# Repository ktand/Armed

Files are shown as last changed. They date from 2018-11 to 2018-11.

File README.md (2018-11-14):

# Armed 3D Printer Controller

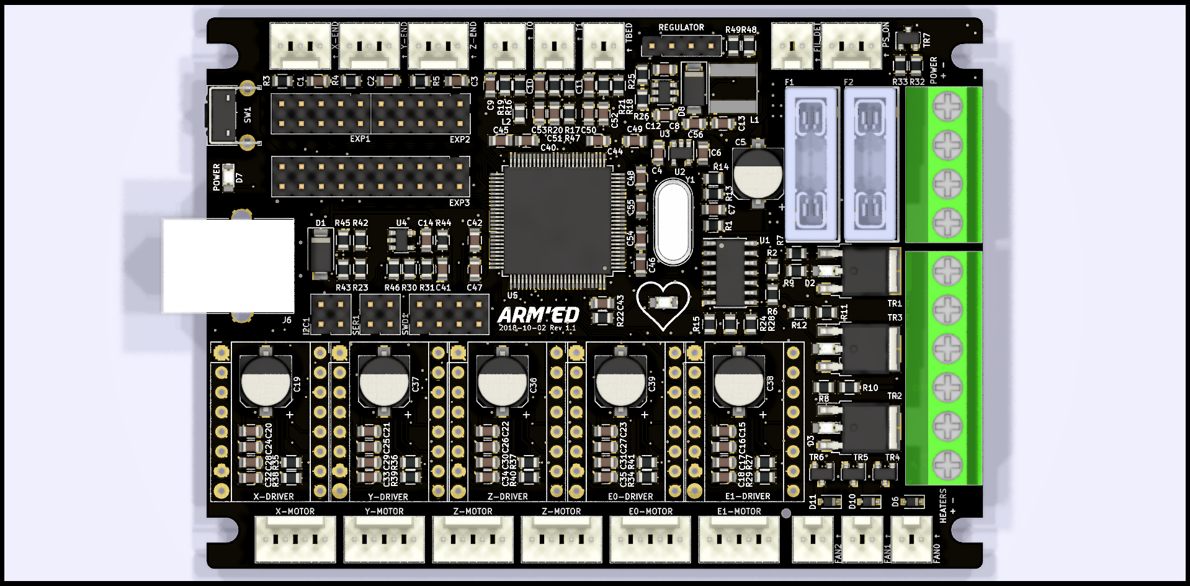
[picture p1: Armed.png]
Armed 1.1


## Features

* 32bit STM32F407VET6 
  * 168MHz 
  * 512kB Flash 
  * 192kB RAM 
* Power supply from 12-24V 
* Dual power inputs with separate fuses 
  * One for one of the high current outputs and the other one for the rest 
* Up to 5 steppers 
  * Dual outputs for one stepper for use with dual stepper Z-axis 
* 3 high current outputs 
* 3 fan outputs 
* 3 temperature sensors inputs 
* 3 endstops inputs 
* Filament runout detection 
* LCD display header 
* USB support 
* 10 extension pins 
* Support for TMC2130 SPI 
* 12-24V supply 
* I2C, SPI and UART extension ports 
* SWD header 
* Stepper configuration using solder jumpers 
* Einsy Rambo Form Factor (100x71mm) 

## Schematic and PCB Design

Designed using [Kicad 5.0](http://kicad-pcb.org/).

## Compatibilty

Arduino compatbile using the [Arduino Core STM32](https://github.com/stm32duino/Arduino_Core_STM32) and working with the [Marlin 2.0 3D printer firmware](https://github.com/MarlinFirmware/Marlin/tree/bugfix-2.0.x).

## Board configuration and pinout

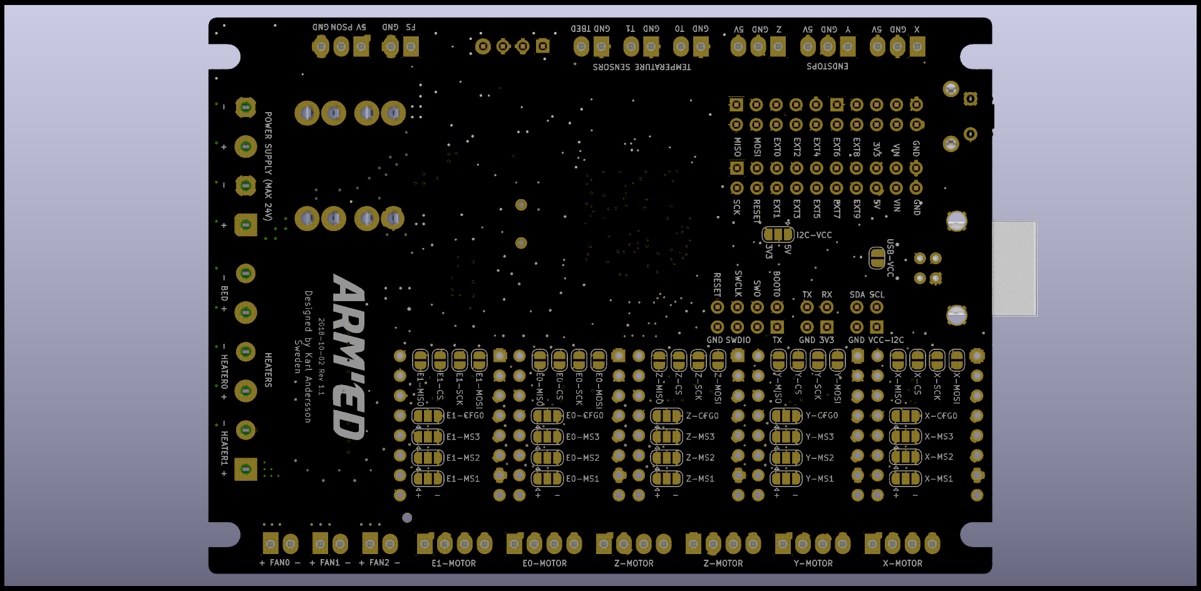
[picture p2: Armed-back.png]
Armed 1.1


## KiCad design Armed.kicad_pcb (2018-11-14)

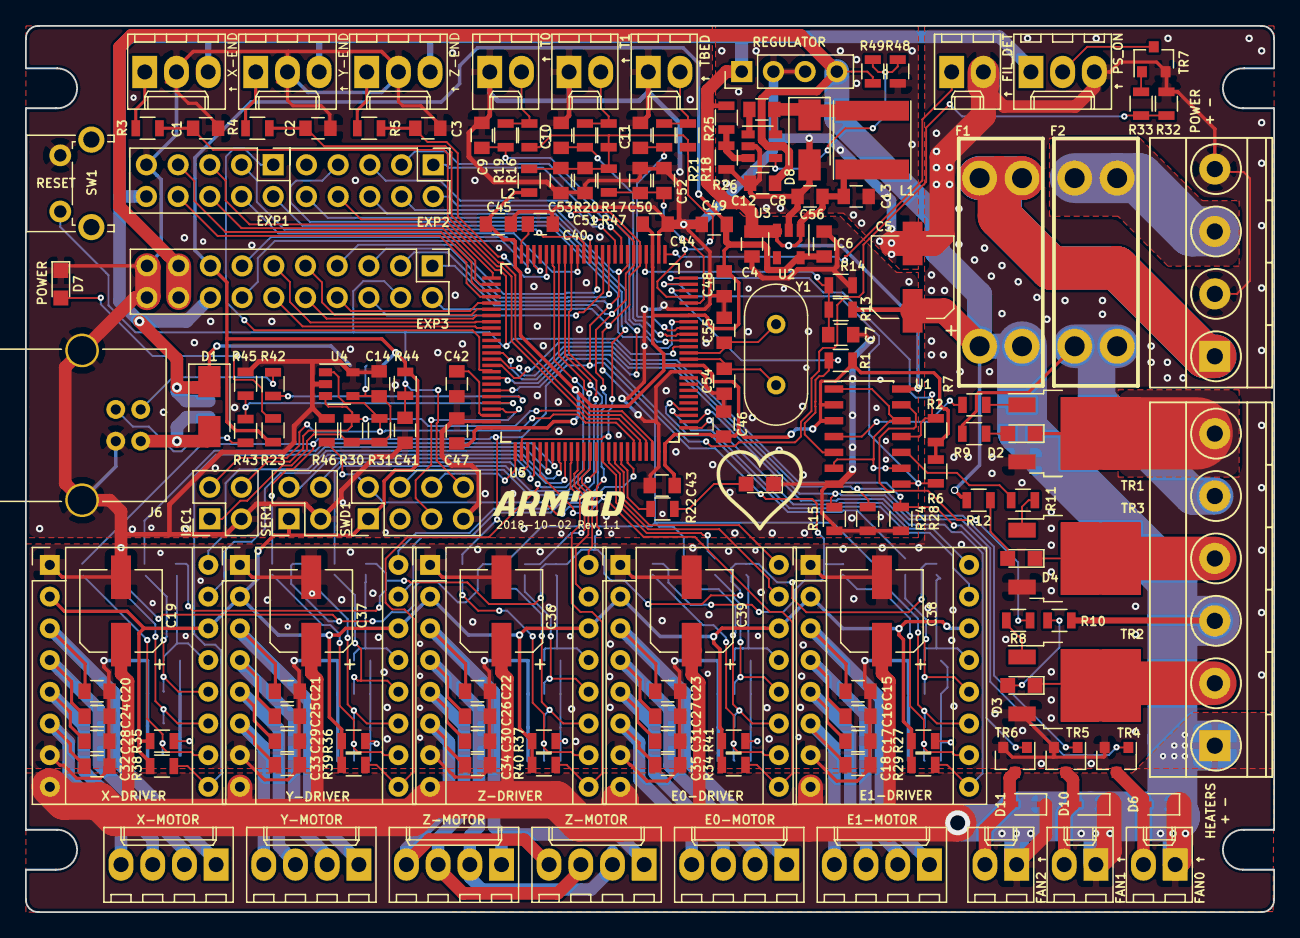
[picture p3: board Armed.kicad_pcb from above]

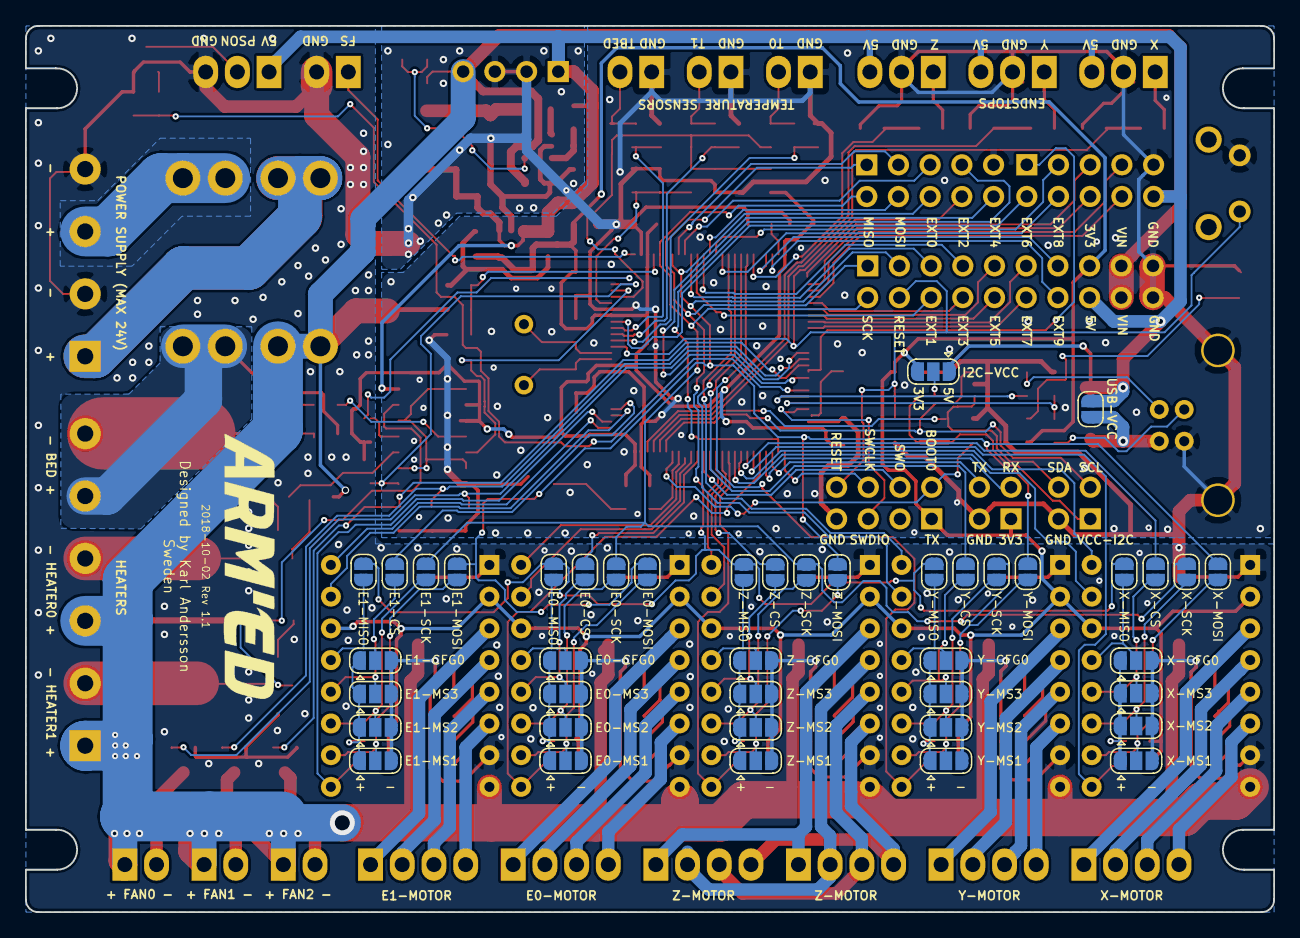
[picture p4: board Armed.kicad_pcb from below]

Board: 2 copper layers, 100.0 x 71.0 mm, 207 parts (42 on the bottom side), 165 nets.

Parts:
A1, A2, A3, A4, A5: Pololu_Breakout_A4988; Pololu_Breakout-16_15.2x20.3mm
C1, C2, C3: 10nF; C_0805
C4, C6: 1uF 16V X7R/X5R; C_0805
C5, C19, C36, C37, C38, C39: 100uF 35V; CP_Elec_6.3x5.8
C7, C12, C14, C41, C43, C44, C45, C46, C47, C48, C52, C53, C56: 100nF; C_0805
C8: 10uF 35V (X5R/X7R); C_0805
C9, C10, C11, C40, C42: 2.2uF; C_0805
C13: 10uF 16V (X5R/X7R); C_0805
C15, C16, C17, C18, C20, C21, C22, C23, C24, C25, C26, C27, C28, C29, C30, C31, C32, C33, C34, C35: 1nF; C_0805
C49: 10uF; C_0805
C50, C51: 1uF; C_0805
C54, C55: 20pF; C_0805
D1: BAT60J; D_SMA
D2, D3, D4, D5, D7: LED; LED_0805
D6, D10, D11: 1N4148WS; D_SOD-323
D8: B140-13-F; D_SMA
E0-MOT1, E1-MOT1: Conn_01x04_Male; Molex_KK-6410-04_04x2.54mm_Straight
EXP1, EXP2: Conn_02x05_Odd_Even; Pin_Header_Straight_2x05_Pitch2.54mm
EXP3: Conn_02x10_Odd_Even; Pin_Header_Straight_2x10_Pitch2.54mm
F1, F2: 3557-2; KEYSTONE-FUSE-3557-2
FAN1, FAN2, FAN3: Conn_01x02; Molex_KK-6410-02_02x2.54mm_Straight
FIL_DET1: Conn_01x02; Molex_KK-6410-02_02x2.54mm_Straight
I2C1: Conn_01x04; Pin_Header_Straight_2x02_Pitch2.54mm
J1: Conn_01x06; TerminalBlock_Phoenix_MKDS1.5-6pol
J2: Conn_01x04; TerminalBlock_Phoenix_MKDS1.5-4pol
J3, J4, J5: Conn_01x03; Molex_KK-6410-03_03x2.54mm_Straight
J6: USB_B
J7: Conn_01x04; Pin_Header_Straight_1x04_Pitch2.54mm
JP1: USB-VCC; SolderJumper-2_P1.3mm_Open_RoundedPad1.0x1.5mm
JP2: E1-MISO; SolderJumper-2_P1.3mm_Open_RoundedPad1.0x1.5mm
JP3: E1-MOSI; SolderJumper-2_P1.3mm_Open_RoundedPad1.0x1.5mm
JP4: E1-SCK; SolderJumper-2_P1.3mm_Open_RoundedPad1.0x1.5mm
JP5: E1-CS; SolderJumper-2_P1.3mm_Open_RoundedPad1.0x1.5mm
JP6: E1-CFG0; SolderJumper-3_P1.3mm_Open_RoundedPad1.0x1.5mm
JP7: E1-MS1; SolderJumper-3_P1.3mm_Open_RoundedPad1.0x1.5mm
JP8: E1-MS2; SolderJumper-3_P1.3mm_Open_RoundedPad1.0x1.5mm
JP9: E1-MS3; SolderJumper-3_P1.3mm_Open_RoundedPad1.0x1.5mm
JP10: E0-MISO; SolderJumper-2_P1.3mm_Open_RoundedPad1.0x1.5mm
JP11: E0-MOSI; SolderJumper-2_P1.3mm_Open_RoundedPad1.0x1.5mm
JP12: E0-SCK; SolderJumper-2_P1.3mm_Open_RoundedPad1.0x1.5mm
JP13: E0-CS; SolderJumper-2_P1.3mm_Open_RoundedPad1.0x1.5mm
JP14: X-MISO; SolderJumper-2_P1.3mm_Open_RoundedPad1.0x1.5mm
JP15: X-MOSI; SolderJumper-2_P1.3mm_Open_RoundedPad1.0x1.5mm
JP16: X-SCK; SolderJumper-2_P1.3mm_Open_RoundedPad1.0x1.5mm
JP17: X-CS; SolderJumper-2_P1.3mm_Open_RoundedPad1.0x1.5mm
JP18: Y-MISO; SolderJumper-2_P1.3mm_Open_RoundedPad1.0x1.5mm
JP19: Y-MOSI; SolderJumper-2_P1.3mm_Open_RoundedPad1.0x1.5mm
JP20: Y-SCK; SolderJumper-2_P1.3mm_Open_RoundedPad1.0x1.5mm
JP21: Y-CS; SolderJumper-2_P1.3mm_Open_RoundedPad1.0x1.5mm
JP22: Z-MISO; SolderJumper-2_P1.3mm_Open_RoundedPad1.0x1.5mm
JP23: Z-MOSI; SolderJumper-2_P1.3mm_Open_RoundedPad1.0x1.5mm
JP24: Z-SCK; SolderJumper-2_P1.3mm_Open_RoundedPad1.0x1.5mm
JP25: Z-CS; SolderJumper-2_P1.3mm_Open_RoundedPad1.0x1.5mm
JP26: E0-CFG0; SolderJumper-3_P1.3mm_Open_RoundedPad1.0x1.5mm
JP27: X-CFG0; SolderJumper-3_P1.3mm_Open_RoundedPad1.0x1.5mm
JP28: Y-CFG0; SolderJumper-3_P1.3mm_Open_RoundedPad1.0x1.5mm
JP29: Z-CFG0; SolderJumper-3_P1.3mm_Open_RoundedPad1.0x1.5mm
JP30: E0-MS1; SolderJumper-3_P1.3mm_Open_RoundedPad1.0x1.5mm
JP31: X-MS1; SolderJumper-3_P1.3mm_Open_RoundedPad1.0x1.5mm
JP32: Y-MS1; SolderJumper-3_P1.3mm_Open_RoundedPad1.0x1.5mm
JP33: Z-MS1; SolderJumper-3_P1.3mm_Open_RoundedPad1.0x1.5mm
JP34: X-MS2; SolderJumper-3_P1.3mm_Open_RoundedPad1.0x1.5mm
JP35: Y-MS2; SolderJumper-3_P1.3mm_Open_RoundedPad1.0x1.5mm
JP36: Z-MS2; SolderJumper-3_P1.3mm_Open_RoundedPad1.0x1.5mm
JP37: E0-MS2; SolderJumper-3_P1.3mm_Open_RoundedPad1.0x1.5mm
JP38: X-MS3; SolderJumper-3_P1.3mm_Open_RoundedPad1.0x1.5mm
JP39: Y-MS3; SolderJumper-3_P1.3mm_Open_RoundedPad1.0x1.5mm
JP40: Z-MS3; SolderJumper-3_P1.3mm_Open_RoundedPad1.0x1.5mm
JP41: E0-MS3; SolderJumper-3_P1.3mm_Open_RoundedPad1.0x1.5mm
JP42: I2C-VCC; SolderJumper-3_P1.3mm_Open_RoundedPad1.0x1.5mm
L1: 22uH NR6028T220M; L_Taiyo-Yuden_NR-60xx
L2: 7427920415; L_0805
PS_ON1: Conn_01x03; Molex_KK-6410-03_03x2.54mm_Straight
R1, R2, R6: 33k; R_0805
R3, R4, R5, R19, R20, R21, R29, R38, R39, R40, R41: 10k; R_0805
R7, R8, R11: 180; R_0805
R9, R10, R12, R14, R16, R17, R18, R27, R30, R31, R34, R35, R36, R37, R45: 4k7; R_0805
R13, R32, R48, R49: 47k; R_0805
R15, R22, R23, R24, R28, R33: 1k; R_0805
R25: 49.9k; R_0805
R26: 9.53k; R_0805
R42, R43: 20; R_0805
R44, R46: 100k; R_0805
R47: 47; R_0805
SER1: Conn_02x02; Pin_Header_Straight_2x02_Pitch2.54mm
SW1: SW_SPST; SW_Tactile_SPST_Angled_PTS645Vx31-2LFS
SWD1: Conn_02X04; Pin_Header_Straight_2x04_Pitch2.54mm
TEMP1, TEMP2, TEMP3: Conn_01x02; Molex_KK-6410-02_02x2.54mm_Straight
TR1, TR2, TR3: IPD036N04L; TO-252-2
TR4, TR5, TR6, TR7: PMV40UN2; SOT-23
U1: 74HCT02; SOIC-14_3.9x8.7mm_Pitch1.27mm
U2: AP2112K-3.3TRG1; SOT-23-5
U3: AOZ1282CI/AP3012; SOT-23-6
U4: 24LC32AT-I/OT; SOT-23-5
U5: STM32F407V(E-G)Tx; LQFP-100_14x14mm_Pitch0.5mm
X-MOT1: Conn_01x04_Male; Molex_KK-6410-04_04x2.54mm_Straight
Y1: 8MHz; Crystal_HC49-U_Vertical
Y-MOT1: Conn_01x04_Male; Molex_KK-6410-04_04x2.54mm_Straight
Z-MOT1, Z-MOT2: Conn_01x04_Male; Molex_KK-6410-04_04x2.54mm_Straight

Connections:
3V3_FAILURE: U1.1, U1.6, U1.9, U1.12
12V1: A1.8, A2.8, A3.8, A4.8, A5.8, C5.1, C8.1, C19.1, C36.1, C37.1, C38.1, C39.1, D6.1, D10.1, D11.1, EXP3.17, EXP3.18, F1.1, FAN1.1, FAN2.1, FAN3.1, J1.1, J1.3, J7.4, R10.2, R12.2, R13.1, R48.2, U3.5
12V2: F2.1, J1.5, R9.2
+3V3: A1.2, A1.14, A2.2, A2.14, A3.2, A3.14, A4.2, A4.14, A5.2, A5.14, C6.1, C43.2, C44.2, C45.2, C46.2, C47.2, C48.2, C49.2, EXP3.15, JP42.3, L2.2, R1.1, R2.1, R6.1, R23.1, R27.2, R29.1, R34.2, R35.2, R36.2, R37.2, R38.1, R39.1, R40.1, R41.1, R44.1, SER1.1, SWD1.1, U1.2, U1.3, U2.5, U5.11, U5.19, U5.28, U5.50, U5.75, U5.100
+5V: C4.1, C13.1, C56.1, D1.1, EXP1.10, EXP3.16, J3.3, J4.3, J5.3, J7.1, JP1.2, JP42.1, L1.1, PS_ON1.1, R25.1, U1.14, U2.1, U2.3
/VCC_I2C: C14.1, I2C1.1, JP42.2, R30.2, R31.2, U4.4
BEEPER_PIN: EXP1.1, U5.66
BOOT0: R46.2, SWD1.2, U5.94
BTN_ENC1: EXP1.2, U5.18
BTN_ENC2: EXP2.3, U5.33
BTN_ENC3: EXP2.5, U5.34
E0_CS_PIN: JP13.1, U5.90
E0_DIR_PIN: A5.16, U5.92
E0_ENABLE_PIN: A5.9, R41.2, U5.80
E0_STEP_PIN: A5.15, U5.91
E1_CS_PIN: JP5.1, U5.4
E1_DIR_PIN: A1.16, U5.1
E1_ENABLE_PIN: A1.9, R29.2, U5.2
E1_STEP_PIN: A1.15, U5.3
EXT0_PIN: EXP3.5, U5.35
EXT1_PIN: EXP3.6, U5.36
EXT2_PIN: EXP3.7, U5.37
EXT3_PIN: EXP3.8, U5.55
EXT4_PIN: EXP3.9, U5.56
EXT5_PIN: EXP3.10, U5.57
EXT6_PIN: EXP3.11, U5.58
EXT7_PIN: EXP3.12, U5.59
EXT8_PIN: EXP3.13, U5.47
EXT9_PIN: EXP3.14, U5.48
FAN0-: D6.2, FAN1.2, TR4.3
FAN0_PIN: R15.1, TR4.1, U5.63
FAN1-: D10.2, FAN2.2, TR5.3
FAN1_PIN: R24.1, TR5.1, U5.64
FAN2-: D11.2, FAN3.2, TR6.3
FAN2_PIN: R28.1, TR6.1, U5.65
FILAMENT_PIN: FIL_DET1.1, U5.26
GND: A1.1, A1.7, A2.1, A2.7, A3.1, A3.7, A4.1, A4.7, A5.1, A5.7, C1.2, C2.2, C3.2, C4.2, C5.2, C6.2, C7.2, C8.2, C9.2, C10.2, C11.2, C13.2, C14.2, C15.2, C16.2, C17.2, C18.2, C19.2, C20.2, C21.2, C22.2, C23.2, C24.2, C25.2, C26.2, C27.2, C28.2, C29.2, C30.2, C31.2, C32.2, C33.2, C34.2, C35.2, C36.2, C37.2, C38.2, C39.2, C40.1, C41.2, C42.1, C43.1, C44.1, C45.1, C46.1, C47.1, C48.1, C49.1, C50.1, C51.2, C52.1, C53.2, C54.1, C55.1, C56.2, D5.1, D7.1, D8.2, EXP1.9, EXP2.9, EXP3.19, EXP3.20, FIL_DET1.2, I2C1.3, J2.2, J2.4, J3.2, J4.2, J5.2, J6.4, J6.5, J7.2, J7.3, JP6.3, JP7.3, JP8.3, JP9.3, JP26.3, JP27.3, JP28.3, JP29.3, JP30.3, JP31.3, JP32.3, JP33.3, JP34.3, JP35.3, JP36.3, JP37.3, JP38.3, JP39.3, JP40.3, JP41.3, PS_ON1.3, R14.2, R15.2, R24.2, R26.2, R28.2, R32.2, R45.1, R46.1, R49.1, SER1.3, SW1.2, SWD1.7, TEMP1.1, TEMP2.1, TEMP3.1, TR1.3, TR2.3, TR3.3, TR4.2, TR5.2, TR6.2, TR7.2, U1.7, U2.2, U3.2, U4.2, U4.5, U5.10, U5.20, U5.27, U5.74, U5.99
HEATBED-: D2.1, J1.6, TR1.2
HEATER0-: D4.1, J1.4, TR3.2
HEATER1-: D3.1, J1.2, TR2.2
HEATER_0_PIN: R6.2, U1.8, U5.24
HEATER_1_PIN: R2.2, U1.11, U5.25
HEATER_BED_PIN: R1.2, U1.5, U5.23
KILL_PIN: EXP2.10, U5.67
LCD_PINS_D4: EXP1.5, U5.51
LCD_PINS_D5: EXP1.6, U5.52
LCD_PINS_D6: EXP1.7, U5.53
LCD_PINS_D7: EXP1.8, U5.54
LCD_PINS_ENABLE: EXP1.3, U5.39
LCD_PINS_RS: EXP1.4, U5.40
LED_PIN: R22.1, U5.93
unnamed: A1.3, C15.1, E1-MOT1.1
unnamed: A1.4, C16.1, E1-MOT1.2
unnamed: A1.5, C17.1, E1-MOT1.3
unnamed: A1.6, C18.1, E1-MOT1.4
unnamed: A1.10, JP3.2, JP7.2
unnamed: A1.11, JP4.2, JP8.2
unnamed: A1.12, JP5.2, JP9.2
unnamed: A1.13, JP2.2, JP6.2
unnamed: A2.3, C20.1, X-MOT1.1
unnamed: A2.4, C24.1, X-MOT1.2
unnamed: A2.5, C28.1, X-MOT1.3
unnamed: A2.6, C32.1, X-MOT1.4
unnamed: A2.10, JP15.2, JP31.2
unnamed: A2.11, JP16.2, JP34.2
unnamed: A2.12, JP17.2, JP38.2
unnamed: A2.13, JP14.2, JP27.2
unnamed: A3.3, C21.1, Y-MOT1.1
unnamed: A3.4, C25.1, Y-MOT1.2
unnamed: A3.5, C29.1, Y-MOT1.3
unnamed: A3.6, C33.1, Y-MOT1.4
unnamed: A3.10, JP19.2, JP32.2
unnamed: A3.11, JP20.2, JP35.2
unnamed: A3.12, JP21.2, JP39.2
unnamed: A3.13, JP18.2, JP28.2
unnamed: A4.3, C22.1, Z-MOT1.1, Z-MOT2.1
unnamed: A4.4, C26.1, Z-MOT1.2, Z-MOT2.2
unnamed: A4.5, C30.1, Z-MOT1.3, Z-MOT2.3
unnamed: A4.6, C34.1, Z-MOT1.4, Z-MOT2.4
unnamed: A4.10, JP23.2, JP33.2
unnamed: A4.11, JP24.2, JP36.2
unnamed: A4.12, JP25.2, JP40.2
unnamed: A4.13, JP22.2, JP29.2
unnamed: A5.3, C23.1, E0-MOT1.1
unnamed: A5.4, C27.1, E0-MOT1.2
unnamed: A5.5, C31.1, E0-MOT1.3
unnamed: A5.6, C35.1, E0-MOT1.4
unnamed: A5.10, JP11.2, JP30.2
unnamed: A5.11, JP12.2, JP37.2
unnamed: A5.12, JP13.2, JP41.2
unnamed: A5.13, JP10.2, JP26.2
unnamed: C12.1, U3.1
unnamed: C12.2, D8.1, L1.2, U3.6
unnamed: C54.2, U5.12, Y1.1
unnamed: C55.2, U5.13, Y1.2
unnamed: D1.2, J6.1, JP1.1
unnamed: D2.2, R9.1
unnamed: D3.2, R10.1
unnamed: D4.2, R12.1
unnamed: D5.2, R22.2
unnamed: D7.2, R23.2
unnamed: J3.1, R3.2
unnamed: J4.1, R4.2
unnamed: J5.1, R5.2
unnamed: JP6.1, JP7.1, JP8.1, JP9.1, R27.1
unnamed: JP26.1, JP30.1, JP37.1, JP41.1, R34.1
unnamed: JP27.1, JP31.1, JP34.1, JP38.1, R35.1
unnamed: JP28.1, JP32.1, JP35.1, JP39.1, R36.1
unnamed: JP29.1, JP33.1, JP36.1, JP40.1, R37.1
unnamed: R7.1, TR1.1
unnamed: R7.2, U1.4
unnamed: R8.1, TR2.1
unnamed: R8.2, U1.13
unnamed: R11.1, TR3.1
unnamed: R11.2, U1.10
unnamed: R16.2, R19.2, TEMP1.2
unnamed: R17.2, R20.2, TEMP2.2
unnamed: R18.2, R21.2, TEMP3.2
unnamed: R25.2, R26.1, U3.3
unnamed: R33.1, TR7.1
unnamed: R42.1, U5.70
unnamed: R43.1, R45.2, U5.71
unnamed: R48.1, R49.2, U3.4
POWER_MONITOR: C7.1, R13.2, R14.1, U5.29
PS_ON: PS_ON1.2, TR7.3
PS_ON_PIN: R32.1, R33.2, U5.69
RESET: C41.1, EXP2.8, EXP3.4, R44.2, SW1.1, SWD1.8, U5.14
RX_PIN: SER1.2, U5.79
SCL: I2C1.2, R31.1, U4.1, U5.95
SDA: I2C1.4, R30.1, U4.3, U5.96
SD_CS: EXP2.4, U5.38
SD_DETECT_PIN: EXP2.7, U5.77
SPI_MISO: EXP2.1, EXP3.1, JP2.1, JP10.1, JP14.1, JP18.1, JP22.1, U5.31
SPI_MOSI: EXP2.6, EXP3.3, JP3.1, JP11.1, JP15.1, JP19.1, JP23.1, U5.32
SPI_SCK: EXP2.2, EXP3.2, JP4.1, JP12.1, JP16.1, JP20.1, JP24.1, U5.30
SWCLK: SWD1.6, U5.76
SWDIO: SWD1.5, U5.72
SWO: SWD1.4, U5.89
TEMP_0_PIN: C9.1, R19.1, U5.15
TEMP_1_PIN: C10.1, R20.1, U5.16
TEMP_2_PIN: C11.1, R21.1, U5.17
TX_PIN: SER1.4, U5.78
USB_DM: J6.2, R42.2
USB_DP: J6.3, R43.2
VCAP_1: C40.2, U5.49
VCAP_2: C42.2, U5.73
VDDA: C51.1, C53.1, L2.1, R16.1, R17.1, R18.1, R47.2, U5.22
VIN1: F1.2, J2.1
VIN2: F2.2, J2.3
VREF+: C50.2, C52.2, R47.1, U5.21
X_CS_PIN: JP17.1, U5.82
X_DIR_PIN: A2.16, U5.83
X_ENABLE_PIN: A2.9, R38.2, U5.81
X_MIN_PIN: C1.1, R3.1, U5.97
X_STEP_PIN: A2.15, U5.84
Y_CS_PIN: JP21.1, U5.43
Y_DIR_PIN: A3.16, U5.41
Y_ENABLE_PIN: A3.9, R39.2, U5.44
Y_MIN_PIN: C2.1, R4.1, U5.98
Y_STEP_PIN: A3.15, U5.42
Z_CS_PIN: JP25.1, U5.86
Z_DIR_PIN: A4.16, U5.88
Z_ENABLE_PIN: A4.9, R40.2, U5.85
Z_MIN_PIN: C3.1, R5.1, U5.45
Z_STEP_PIN: A4.15, U5.87

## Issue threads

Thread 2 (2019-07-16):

Kicad schematic shows errors when opening

xebbmw, 2019-07-16:
Hi,

When I am trying to open the schematic file using Kicad 5, there are error messages showing libraries missing:
Armed-rescue.lib
object-technologies.lib

Could you please upload the above libraries to Github?

zedthirteen, 2020-03-25:
I am also having this issue with missing libraries

ktand, 2020-12-21:
I will add the missing files in the next few days!

zedthirteen, 2020-12-21:
Really nice to hear from you Karl.

I love your design. Thanks for all of your efforts.I certainly will appreciate the missing files. I was able to map many of the components to standard library items but not the FETs or the STM32 :-(

Should my i2c voltage be 3.3 or 5v?  My PC is in for repair just now, so not sure where I got to,  but I think I tried 3.3v and the writes failed - might be due to some other error though

Thanks again
Regards
David

Sent from my iPhone

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

ktand, 2020-12-21:
Sorry for missing all the notifications. They got buried in all other
github-notifications. I'll try to be more responsive!

I'm running the EEPROM @ 3.3V - with everything working.

Den mån 21 dec. 2020 kl 10:56 skrev David <notifications@github.com>:

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

zedthirteen, 2021-01-22:
Hi Karl, sorry to nag - but any news on those missing libraries? Are you having to recreate them?

one of them was in  C:/Users/Karl/PCB-designs/KiCad/Libraries/object-technologies.lib on your PC. The armed-rescue.lib file has environment variables in its embedded file name so I can't help with that one.  I think the object-technologies library had the missing STM32 component.   I think armed-rescue had many missing items including BSH105 and IPD036N04L.

I managed to find suitable standard library or alternative symbols for all except the STM32F407, BSH105 and IPD036N04L

ktand, 2021-01-22:
Sorry, I have updated the schematic to use the armed.lib library (commit c9e9fdd157b36a4a59312abd6035c331b24d473f). The armed.lib now contains the referenced symbols from object-technologies.lib. Please let me know if it works for you.

zedthirteen, 2021-01-22:
looks perfect now. Opens without errors and I can now see which processor pins connect to which signals - thanks :-)

Closed 2021-01-22.

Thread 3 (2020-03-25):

Other resources?

zedthirteen, 2020-03-25:
More a few questions rather than issues. Sorry to post them here but there isn't a lot of info on the web (or I can't find it)

Are there links to resources on how to load from VS code/Platformio to the board. My last 32 bit board used a firmware.bin file on microsd but this isn't possible.

Any links to how to connect text or graphic display modules to EXP1/EXP2? There isn't room to get the two headers on from my RepRapDiscount Smart Controller. I'm loading KiCad now to try to look at the schematics to try and understand pinouts. I will try to connect through 20 pin IDC connector.

Also, there are a lot of undocumented solder bridge points on the underside of the board. Any descriptions for these? I need to configure for FYSTEC TMC2130's for sensorless homing. Perhaps KiCad schematic will help me with these once I get it up and running

NB. I have KiCad installed now but I think too much information is missing from schematic without the missing lib files

ktand, 2021-01-22:
The missing libraries issue is fixed.

Closed 2021-01-22.

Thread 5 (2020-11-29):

Support STM32 Armed

BorPass, 2020-11-29:
Dear Karl, dear community,
I want to replace my old gt2560 printer board with this STM32 Armed board.
I managed to compile Marlin 2.0 for the board with arduino ide and uploaded with STM32CubeProgrammer.
The problem I am currently facing and for which can‘t find a solution is, that I can‘t get access to the board through usb-port using octoprint, which is my print-server.

What I did so far:

1. I uploaded a blink sketch the same way I uploaded Marlin, in order to check my upload process. It worked, the heartbeat led is blinking!
2. Marlin compiles without errors. Therefore I guess the hex-file it creates is correct. By the way, I used Serial_Port -1 in configuration.h, which was the only configuration that compiled without errors.
3. dmesg shows the usb-port of my armed board as /dev/ttyACM0

Do you have any ideas, what else I could check in order to find the problem or which files I should share to give you a hint to the problem.

Another question:
Is there a description of how to connect a lcd display to the board.

Best Regards

ktand, 2020-12-30:
Did you configure Marlin to use the USB serial port?

BorPass, 2020-12-30:
Hello Karl, thanks for the reply. I discussed my issue under the subject of David (zedthirteen), with whom you had contact in the last days.
My current status is:
- usb works
- Simulated eeprom works, real eeprom not, because the chip is missing on my board. I‘m pretty sure real eeprom will work, as soon as I soldered the already ordered chip.
- I still have problems with the watchdog- part of Marlin. It causes my board to restart every few seconds - commenting it out, it works. I will check your 2.0.7 version of Marlin tomorrow for differences to my current version.
- More work will have to be done for me on using tmc2208 in uart mode. Should this work and if yes, do you have any advice if I have to solder bridges like David did for making his tmc-stepper work in spi mode?

I think I‘m on the way to success...

It would be perfekt, if you publish some kind of manual for several details, e.g the ones I found in the pins_ARMED.h concerning the rx/tx pins for stepper-communication. It would be useful to have this in the board documentation here, perhaps together with a hint, why rx and tx is the same pin. As far as I thought to know, you need them separate, but I did not read enough about that. Information on the purpose of the several soldering bridge possibilities would be great, too, especially, because they are very board-specific.

Anyway, the more I understand about your board, the more I like it.

But it is still some way to go for me, until it will work like I want it to do.

Best Regards,
Boris

ktand, 2021-01-22:
Hi, sorry, no manual is planned at this time.

Maybe you can get some help from the configuration I'm using. (TMC2209), please take look at my Marlin branch here https://github.com/ktand/Marlin/tree/2.0.7.2-armed-12864-2020-11-05

Closed 2021-01-22.

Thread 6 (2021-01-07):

Fan control

zedthirteen, 2021-01-07:
Does fan control work?

Or, am I missing something in the way I am connecting the fan or some extra required configuration perhaps?

My TMC2130's are overheating so I added a 24V fan to the electronics door, connected to FAN0 (also tried both FAN1 and FAN2) but I was unable to get it to work. My board has 24V supply.

I tried sending fan control g-code commands (M106 P0 S255 and other variations) but was unable to get the fan to activate.  I have since hardwired the fan to 24V supply but would rather have control over it if possible.

ktand, 2021-04-15:
Fan control works. Make sure you build Marlin using the latest Platform IO. There was a problem with the board definition in an earlier release of PlatformIO / Arduino Core STM32 that caused a fan control issue.

zedthirteen, 2021-04-15:
Thanks for feedback. I will try as you suggest

zedthirteen, 2021-06-24:
Finally found some time to experiment with builds.
Still having a couple of problems - using your fork (2.0.8.2-armed-12864-2021-06-01) and my configuration(adv).h files. To the best of my knowledge PlatformIO is up to date, I always agree to update and restart. Core is 5.1.1, Home is 3.3.4

Build will not let use "#define NUM_M106_FANS 3" - will only allow value of 1.
Conditionals_post.h is only defining "#define HAS_FAN0 1" - all others are grayed out. However pins_ARMED.h has FAN_PIN, FAN1_PIN and FAN2_PIN configured as PC6, PC7 & PC8.

Other issue is that if I enable #define SPEAKER I get a timer conflict.  I don't know if it is related to the fan issue or because I'm using TMC2130 drivers. I can live without speaker though.

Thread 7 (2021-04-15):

New board

milicigoran, 2021-04-15:
Sorry if its a dumb question but I picked up this board for the price and saw it could work with a prusa. I have a mk3s prusa but SS the MB and until the new one gets here it will be some time so i ordered this and it got here in a few days. But i cant find much instructions on it or other marlin files so i kind of know what to flash . Or if i can even flash ince it seems like the bootloader is locked or doesn't have one. See am just guessing flying blind here. Any help would be awesome.

ktand, 2021-04-15:
You just have to build Marlin using the PlatformIO environment (preferably using VS Code) and then you upload the firmware to the board.

milicigoran, 2021-04-17:
Is there a configuration anywhere to get a kind of jumpstart or just start from zero? Because I'm trying to use it for a prusa i3 mk3s like it says in the description that it can be a drop in replacement but i have no clue if it came preloaded with the firmware or i have to build it from scratch. really no info out there on this board. When i plug it in the red light just blinks.

milicigoran, 2021-04-17:
would this would probably work if i took the skr 1.4 turbo prusa fork and just changed the environment to this board?

milicigoran, 2021-04-18:
I tried that last night without much success. I think i had the proper
environment except i had problems with the accompanying header files .
Either they werent there or were wrong or outdated. It wouldn't let me
build with tmc 2009 but when I switched to tmc 2130 8t let me go almost to
the end of compiling before some new error messages. You dont happened to
have a copy of a compiled config.h and config.adv.h you could email so I
could just plug in to try and take a look over it and see what kind of
works and what doesn't. This is my first board that's not mainstream that
has a ton of documentation. But would love to be able to use it amd not
spend 90 bucks for einsy Rambo boards

On Wed, Apr 14, 2021, 11:11 PM Karl Andersson ***@***.***>
wrote:

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

logan8888, 2021-12-14:
I am trying to use this board but my windows 10 PC does not recognize it.....Do i need to get a driver from somewhere?

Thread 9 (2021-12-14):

Driver?

logan8888, 2021-12-14:
Do i need  a specific driver for this board? My Windows Pc doesn't seem to recognise it?

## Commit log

2018-11-14 Armed 1.0 Schematic/PCB
    [Armed.kicad_pcb, Armed.sch, file5A7E008D.sch]
2018-11-14 Armed 1.0 Board rendering
2018-11-14 Armed 1.1
    [Armed.kicad_pcb, Armed.sch, file5A7E008D.sch]
2018-11-14 Updated board images
2021-01-22 Fixed library references
    [Armed.sch, file5A7E008D.sch]
